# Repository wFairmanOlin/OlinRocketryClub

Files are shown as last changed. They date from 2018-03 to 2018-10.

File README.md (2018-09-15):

# OlinRocketryClub
Repo for a self-designed flight computer

## First Project - Phoenix I
1. 3-axis accelerometer
2. data storing functionality to SD card

## Second Project - Peregrine I
This board is intended to record flight data and transmit telemetry while maintaining a slim and lightweight profile.

### Main Components:
1. Barometer, Accelerometer, Gyroscope
2. Data storage to SD card
3. RF Transmitter
4. Battery

## How to Clone this Repo (Ubuntu)
1. Use the Ctrl+Alt+t command to open your terminal. 
2. Use the `cd` command to switch to the directory you want to save this repo in.
3. Copy and paste the code below into your terminal (hint: use Ctrl+Shift+v to paste into the terminal)
```
git clone https://github.com/wFairmanOlin/OlinRocketryClub.git
```

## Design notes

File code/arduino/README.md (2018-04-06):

## Most recent update
4/6/2018 This program currently only contains code for logging data to the SD card. 
We are successfully accessing IMU data, but we are having issues with the SD card reader 
itself - even the arduino example script will not run, suggesting there is a hardware or
wiring problem involved that needs to be resolve.

## REMAINING TODOS
  - Research and program apogee detection and decide how best to implement that. 
    Possibilities include integrating accelerometer data and relying on orientation of the IMU.
    For now, simply send power to a single pin to simulate releasing the parachute.
  - Acquire, prototype, and implement using a radio transmitter and receiver to send and receive RF beacon style data
  - Acquire, prototype, and implement using a radio transmitter and receiver to send and receive telemetry information.
  - Discretize steps into functions as soon as proof of concept has been achieved.

# Arduino Sketch
Prior to fabricating and testing a PCB for the rocket flight computer, we hope to create an arduino model of the system for base-level systems testing. To do so, we hope to write a quick arduino program, wire necessary hardware, and simulate a launch.

## The main goals of flight_computer.ino are:
1. Use an inertial measurement unit to determine when the rocket has reached apogee. When that has happened (i.e. when the velocity of the rocket is zero), deploy
        the parachute. 
2. Log telemetry data to the onboard SD card for study following retrieval. 
3. Use a radio transmitter as an RF beacon to aid retrieval efforts.
4. Use a radio transmitter to send telemetry data by means of packet radio. 

## The hardware components associated with this test include:
BreadBoard Components:
-accelerometer - https://www.adafruit.com/product/2019
-sd card slot  - https://www.sparkfun.com/products/544
-arduino uno - https://www.sparkfun.com/products/11021
-Breakout Radio Chips (2) - https://www.sparkfun.com/products/12775
-Sparkfun RF Link Transmitter - https://www.sparkfun.com/products/10534
-Sparkfun RF Link Receiver - https://www.sparkfun.com/products/10532

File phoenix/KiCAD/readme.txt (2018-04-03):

 

**********************************************************
*************  Important Instructions Follow  ************
**********************************************************
 
All files exported to: C:\EMA\ExportFolder\0\188490\Output\KiCAD\KiCAD\symbols.lib

After you have used Ultra Librarian to export library:
**************************************************
**To import your new library symbols into KiCad:**
**************************************************
1. Open KiCad.
2. On the program/tool list, go to Eeschema.
3. Select *Preferences* from the menu bar then select *Library*.
4. Click *Add* and choose the newly exported *.LIB* file.
5. You have now successfully imported your new symbol library!

**************************************************************
**To import your new library footprints/patterns into KiCad:**
**************************************************************
1. Open KiCad.
2. On the program/tool list, go to Pcbnew.
3. Follow the same steps as you would importing symbols, only this time select the *.kicad_mod* file.
4. You have now successfully imported your new footprint/pattern.

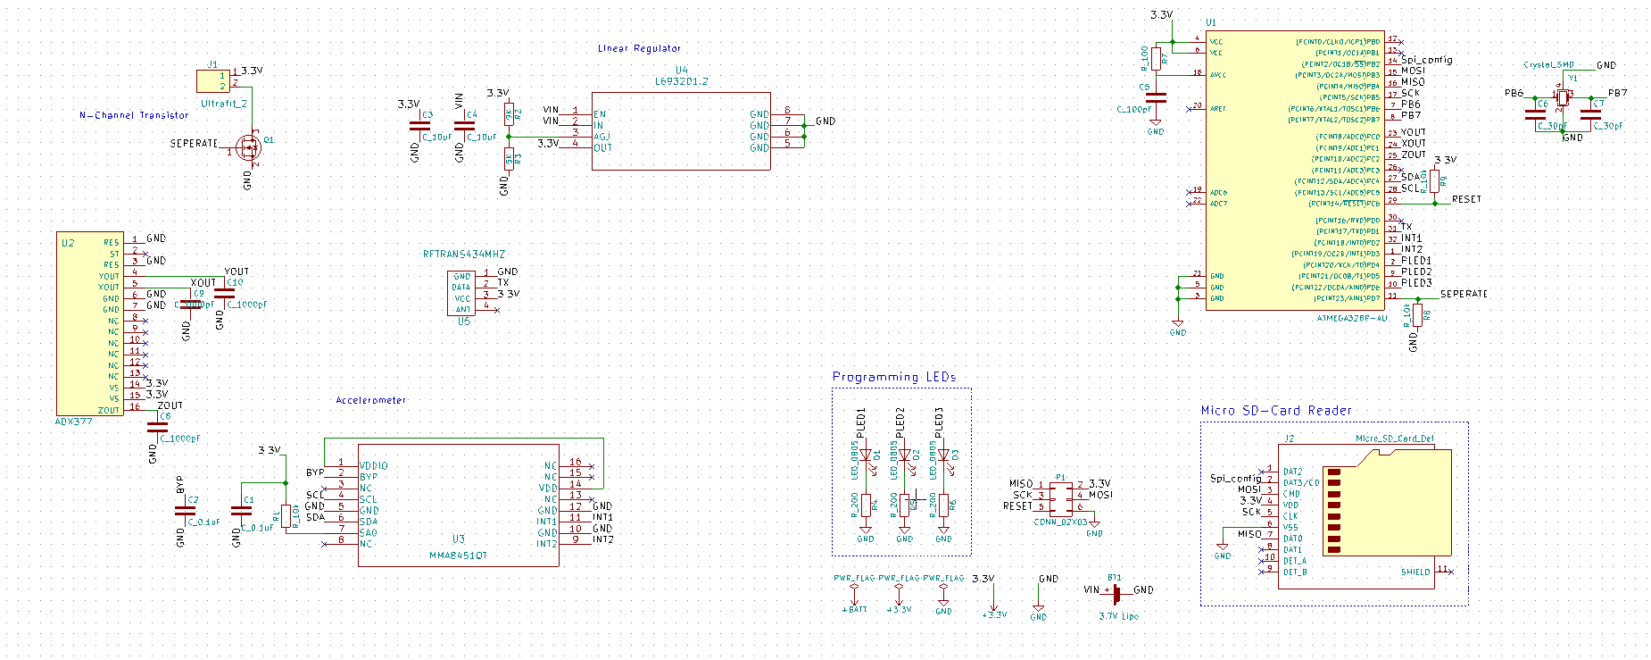
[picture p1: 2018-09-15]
phoenix/Schematic.png

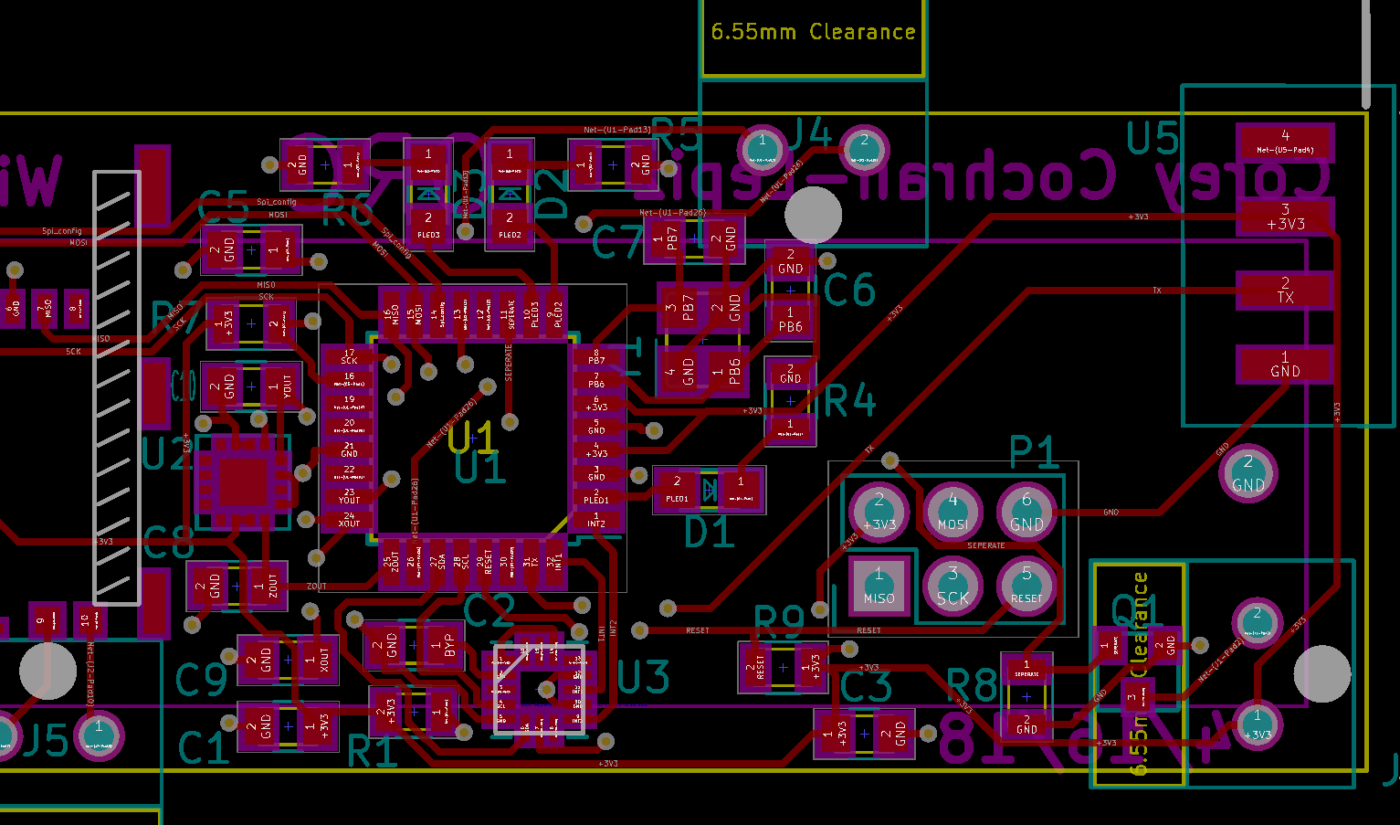
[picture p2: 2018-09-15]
phoenix/board.png

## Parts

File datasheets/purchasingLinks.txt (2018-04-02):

Purchasing Links
sd card slot  - https://www.digikey.com/product-detail/en/molex-llc/5045280892/WM12730CT-ND/5822266
gps chip      - https://www.adafruit.com/product/746
3.3V stepdown - https://www.digikey.com/product-detail/en/on-semiconductor/FAN5362UMP33X/FAN5362UMP33XCT-ND/3908079
--Option 2    - https://www.digikey.com/product-detail/en/stmicroelectronics/L6932D1.2TR/497-5724-1-ND/1299970
battery holder- https://www.digikey.com/product-detail/en/mpd-memory-protection-devices/BCAAPC/BCAAPC-ND/232723
MOSFET	      - https://www.digikey.com/product-detail/en/vishay-siliconix/SI4838DY-T1-E3/SI4838DY-T1-E3TR-ND/1656477
Batteries and
Charger       - https://www.amazon.com/EBL-Battery-Charger-Rechargeable-Batteries/dp/B076C4K4SR
MicroSD Card
Slot 	      - https://www.digikey.com/product-detail/en/molex-llc/5045280892/WM12730CT-ND/5822266

BreadBoard Components:
accelerometer - https://www.adafruit.com/product/2019
sd card slot  - https://www.sparkfun.com/products/544
cpu (sparkFun)- https://www.sparkfun.com/products/9061
AVR Programmer- https://www.sparkfun.com/products/9825
Breakout Radio Chips (need 2) - https://www.sparkfun.com/products/12775
Sparkfun RF Link Transmitter - https://www.sparkfun.com/products/10534
Sparkfun RF Link Receiver - https://www.sparkfun.com/products/10532

Spark plug via mosfet
http://forum.arduino.cc/index.php?topic=95811.0

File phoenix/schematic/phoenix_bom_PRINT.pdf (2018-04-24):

phoenix_bom_PRINT

Component | References Value | Quantity Per PCB
1 BT1 | 3.7V Lipo | 1
2 C1 C2 | C_0.1uF | 2
3 C8 C9 C10 C_1000pF | 3
4 C5 | C_100pF | 1
5 C3 C4 | C_10uF | 2
6 C6 C7 | C_30pF | 2
7 D1 D2 D3 | LED_0805 | 3
8J2 | Micro_SD_Card_Det | 1
9J1 | Ultrafit_2 | 1
10 P1 | CONN_02X03 | 1
11 Q1 | IRLML6344 | 1
12 R3 | 5K | 1
13 R2 | 9K | 1
14 R7 | R_100 | 1
15 R1 R8 R9 | R_10k | 3
16 R4 R5 R6 | R_200 | 3
17 U2 | ADX377 | 1
18 U1 | ATMEGA328P-AU | 1
19 U4 | L6932D1.2 | 1
20 U3 | MMA8451QT | 1
21 U5 | RFTRANS434MHZ | 1
22 Y1 | Crystal_SMD | 1

Component Groups:
Component Count:
Fitted Components:
Number of PCBs:
Total components:
Schematic Version:
Schematic Date:
BoM Date:
Schematic Source:
KiCad Version:

Datasheet | Package
http://datasheets.avx.com/X7RDielectric.pdf | Value
| Value
https://content.kemet.com/datasheets/KEM_C1003_C0G_SMD.pdf | Value
http://datasheets.avx.com/cx5r.pdf | Value
https://media.digikey.com/pdf/Data%20Sheets/Samsung%20PDFs/CL_Series_MLCC_ds.pdf Value
http://www.osram-os.com/Graphics/XPic9/00078860_0.pdf | Value
| Value
http://portal.fciconnect.com/Comergent//fci/drawing/67996.pdf | Value
https://www.infineon.com/dgdl/irlml6344pbf.pdf?fileId=5546d462533600a4015356689c44262c
https://www.seielect.com/Catalog/SEI-rncp.pdf | Value
http://www.bourns.com/data/global/pdfs/CRS.pdf | Value
https://www.seielect.com/Catalog/SEI-RMCF_RMCP.pdf | Value
https://support.epson.biz/td/api/doc_check.php?dl=brief_FA-238V_en.pdf | Value

MPN | MFN
478-3352-1-ND | Digi-Key
1276-6843-1-ND | Digi-Key
399-1122-1-ND | Digi-Key
478-5167-1-ND | Digi-Key
1276-1130-1-ND | Digi-Key
475-1410-1-ND | Digi-Key
WM11570-ND | Digi-Key
609-3234-ND | Digi-Key
RNCP0805FTD100RCT-ND | Digi-Key
CRS0805-FX-1002ELFCT-ND Digi-Key
RMCF0805JT200RCT-ND | Digi-Key
SER3686CT-ND | Digi-Key

PurchasingLink

https://www.digikey.com/products/en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

https://www.digikey.com/product-detail/en/molex-llc/1722861102/WM11570-ND/5344267https://www.digikey.com/product-detail/en/amphenol-fci/67997-206HLF/609-3234-ND/1878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

https://www.digikey.com/products/en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

https://www.digikey.com/products/en?keywords=SER3686CT-ND

PurchasingLinks

https://www.digikey.com/product-detail/en/infineon-technologies/IRLML6344TRPBF/IRLML6344TRPBFCT-ND/2538168

https://www.digikey.com/product-detail/en/analog-devices-inc/ADXL377BCPZ-RL7/ADXL377BCPZ-RL7CT-ND/3678489

https://www.digikey.com/products/en?mpart=MMA8451QT&v=568
https://www.sparkfun.com/products/10534

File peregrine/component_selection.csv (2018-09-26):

-------------------+-----------------+---------+------------------------+----------------+---------------------------
Component | Function | Price | Communication protocol | Max power draw | Notes
-------------------+-----------------+---------+------------------------+----------------+---------------------------
Atmel328PB | Microcontroller | 1.46/ea | n/a | 10mA@5v0
BMI088 | Accel+Gyro | 7.99/ea | SPI & I2C | 5.5mA@3v3 | gucci vibration rejection
ICG-20660L | Accel+Gyro | 8.27/ea | SPI & I2C | 3mA@3v3 | maybe ew????
BMP388 | Barometer | 3.93/ea | SPI & I2C | 0.68mA@3v3
MIC5504-3.3YM5-TR | 3v3 LDO | 0.11/ea | Screeching | 300mA | cheap!
-------------------+-----------------+---------+------------------------+----------------+---------------------------
 |  | 21.75 |  | <20mA
-------------------+-----------------+---------+------------------------+----------------+---------------------------

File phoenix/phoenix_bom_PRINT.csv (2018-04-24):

Component | References | Value | Quantity Per PCB | Datasheet | Package | MPN | MFN | PurchasingLink | PurchasingLinks
1 | BT1 | 3.7V Lipo | 1
2 | C1 C2 | C_0.1uF | 2 | http://datasheets.avx.com/X7RDielectric.pdf | Value | 478-3352-1-ND | Digi-Key | https://www.digikey.com/products/en?keywords=478-3352-1-ND
3 | C8 C9 C10 | C_1000pF | 3 |  | Value | 1276-6843-1-ND | Digi-Key | https://www.digikey.com/product-detail/en/samsung-electro-mechanics/CL21B102KB6WPNC/1276-6843-1-ND/5961702
4 | C5 | C_100pF | 1 | https://content.kemet.com/datasheets/KEM_C1003_C0G_SMD.pdf | Value | 399-1122-1-ND | Digi-Key | https://www.digikey.com/product-detail/en/kemet/C0805C101J5GACTU/399-1122-1-ND/411397
5 | C3 C4 | C_10uF | 2 | http://datasheets.avx.com/cx5r.pdf | Value | 478-5167-1-ND | Digi-Key | https://www.digikey.com/product-detail/en/avx-corporation/0805ZD106KAT2A/478-5167-1-ND/1913257
6 | C6 C7 | C_30pF | 2 | https://media.digikey.com/pdf/Data%20Sheets/Samsung%20PDFs/CL_Series_MLCC_ds.pdf | Value | 1276-1130-1-ND | Digi-Key | https://www.digikey.com/product-detail/en/samsung-electro-mechanics-america-inc/CL21C300JBANNNC/1276-1130-1-ND/3889216
7 | D1 D2 D3 | LED_0805 | 3 | http://www.osram-os.com/Graphics/XPic9/00078860_0.pdf | Value | 475-1410-1-ND | Digi-Key | https://www.digikey.com/products/en?keywords=475-1410-1-ND
8 | J2 | Micro_SD_Card_Det | 1
9 | J1 | Ultrafit_2 | 1 |  | Value | WM11570-ND | Digi-Key | https://www.digikey.com/product-detail/en/molex-llc/1722861102/WM11570-ND/5344267
10 | P1 | CONN_02X03 | 1 | http://portal.fciconnect.com/Comergent//fci/drawing/67996.pdf | Value | 609-3234-ND | Digi-Key | https://www.digikey.com/product-detail/en/amphenol-fci/67997-206HLF/609-3234-ND/1878491
11 | Q1 | IRLML6344 | 1 | https://www.infineon.com/dgdl/irlml6344pbf.pdf?fileId=5546d462533600a4015356689c44262c |  |  |  |  | https://www.digikey.com/product-detail/en/infineon-technologies/IRLML6344TRPBF/IRLML6344TRPBFCT-ND/2538168
12 | R3 | 5K | 1
13 | R2 | 9K | 1
14 | R7 | R_100 | 1 | https://www.seielect.com/Catalog/SEI-rncp.pdf | Value | RNCP0805FTD100RCT-ND | Digi-Key | https://www.digikey.com/products/en?keywords=RNCP0805FTD100RCT-ND
15 | R1 R8 R9 | R_10k | 3 | http://www.bourns.com/data/global/pdfs/CRS.pdf | Value | CRS0805-FX-1002ELFCT-ND | Digi-Key | https://www.digikey.com/products/en?keywords=CRS0805-FX-1002ELFCT-ND
16 | R4 R5 R6 | R_200 | 3 | https://www.seielect.com/Catalog/SEI-RMCF_RMCP.pdf | Value | RMCF0805JT200RCT-ND | Digi-Key | https://www.digikey.com/products/en?keywords=RMCF0805JT200RCT-ND
17 | U2 | ADX377 | 1 |  |  |  |  |  | https://www.digikey.com/product-detail/en/analog-devices-inc/ADXL377BCPZ-RL7/ADXL377BCPZ-RL7CT-ND/3678489
18 | U1 | ATMEGA328P-AU | 1
19 | U4 | L6932D1.2 | 1
20 | U3 | MMA8451QT | 1 |  |  |  |  |  | https://www.digikey.com/products/en?mpart=MMA8451QT&v=568
21 | U5 | RFTRANS434MHZ | 1 |  |  |  |  |  | https://www.sparkfun.com/products/10534
22 | Y1 | Crystal_SMD | 1 | https://support.epson.biz/td/api/doc_check.php?dl=brief_FA-238V_en.pdf | Value | SER3686CT-ND | Digi-Key | https://www.digikey.com/products/en?keywords=SER3686CT-ND
Component Groups:
Component Count:
Fitted Components:
Number of PCBs:
Total components:
Schematic Version:
Schematic Date:
BoM Date:
Schematic Source:
KiCad Version:

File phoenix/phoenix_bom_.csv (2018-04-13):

Component | Description | Part | References | Value | Footprint | Quantity Per PCB | Datasheet | Package | MPN | MFN | PurchasingLink | PurchasingLinks
1 | single battery cell | Battery_Cell | BT1 | 3.7V Lipo | battery_holder | 1
2 |  | C_0.1uF | C1 C2 | C_0.1uF | C_0805_OEM | 2 | http://datasheets.avx.com/X7RDielectric.pdf | Value | 478-3352-1-ND | Digi-Key | https://www.digikey.com/products/en?keywords=478-3352-1-ND
3 |  | C_100pF | C5 | C_100pF | C_0805_OEM | 1 | https://content.kemet.com/datasheets/KEM_C1003_C0G_SMD.pdf | Value | 399-1122-1-ND | Digi-Key | https://www.digikey.com/product-detail/en/kemet/C0805C101J5GACTU/399-1122-1-ND/411397
4 |  | C_10uF | C3 C4 | C_10uF | C_0805_OEM | 2 | http://datasheets.avx.com/cx5r.pdf | Value | 478-5167-1-ND | Digi-Key | https://www.digikey.com/product-detail/en/avx-corporation/0805ZD106KAT2A/478-5167-1-ND/1913257
5 |  | C_30pF | C6 C7 | C_30pF | C_0805_OEM | 2 | https://media.digikey.com/pdf/Data%20Sheets/Samsung%20PDFs/CL_Series_MLCC_ds.pdf | Value | 1276-1130-1-ND | Digi-Key | https://www.digikey.com/product-detail/en/samsung-electro-mechanics-america-inc/CL21C300JBANNNC/1276-1130-1-ND/3889216
6 |  | LED_0805 | D1 D2 D3 | LED_0805 | LED_0805_OEM | 3 | http://www.osram-os.com/Graphics/XPic9/00078860_0.pdf | Value | 475-1410-1-ND | Digi-Key | https://www.digikey.com/products/en?keywords=475-1410-1-ND
7 | Micro SD Card Socket with card detection pins | Micro_SD_Card_Det | J2 | Micro_SD_Card_Det | SD-Card | 1 | https://www.hirose.com/product/en/download_file/key_name/DM3/category/Catalog/doc_file_id/49662/?item_id=195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
8 |  | Ultrafit_2 | J1 | Ultrafit_2 | Ultrafit_2_RA | 1 |  | Value | WM11570-ND | Digi-Key | https://www.digikey.com/product-detail/en/molex-llc/1722861102/WM11570-ND/5344267
9 |  | CONN_02X03 | P1 | CONN_02X03 | Pin_Header_Straight_2x03 | 1 | http://portal.fciconnect.com/Comergent//fci/drawing/67996.pdf | Value | 609-3234-ND | Digi-Key | https://www.digikey.com/product-detail/en/amphenol-fci/67997-206HLF/609-3234-ND/1878491
10 | 200V Vds, N-Channel MOSFET, 2.6V Logic Level, TO-92 | IRLML6344 | Q1 | IRLML6344 | IRLML6344TRPBFCT-ND | 1 | https://www.infineon.com/dgdl/irlml6344pbf.pdf?fileId=5546d462533600a4015356689c44262c |  |  |  |  | https://www.digikey.com/product-detail/en/infineon-technologies/IRLML6344TRPBF/IRLML6344TRPBFCT-ND/2538168
11 |  | 5K | R3 | 5K | R_0805_OEM | 1
12 |  | 5K | R2 | 9K | R_0805_OEM | 1
13 |  | R_100 | R7 | R_100 | R_0805_OEM | 1 | https://www.seielect.com/Catalog/SEI-rncp.pdf | Value | RNCP0805FTD100RCT-ND | Digi-Key | https://www.digikey.com/products/en?keywords=RNCP0805FTD100RCT-ND
14 |  | R_10k | R1 R8 R9 | R_10k | R_0805_OEM | 3 | http://www.bourns.com/data/global/pdfs/CRS.pdf | Value | CRS0805-FX-1002ELFCT-ND | Digi-Key | https://www.digikey.com/products/en?keywords=CRS0805-FX-1002ELFCT-ND
15 |  | R_200 | R4 R5 R6 | R_200 | R_0805_OEM | 3 | https://www.seielect.com/Catalog/SEI-RMCF_RMCP.pdf | Value | RMCF0805JT200RCT-ND | Digi-Key | https://www.digikey.com/products/en?keywords=RMCF0805JT200RCT-ND
16 | TQFP32, 16k Flash, 1kB SRAM, 512B EEPROM | ATMEGA328P-AU | U1 | ATMEGA328P-AU | TQFP-32_7x7mm_Pitch0.8mm | 1 | http://www.atmel.com/images/atmel-8271-8-bit-avr-microcontroller-atmega48a-48pa-88a-88pa-168a-168pa-328-328p_datasheet.pdf
17 |  | L6932D1.2 | U4 | L6932D1.2 | L6932D1.2TR | 1
18 |  | MMA8451QT | U3 | MMA8451QT | MMA8451QT | 1 |  |  |  |  |  | https://www.digikey.com/products/en?mpart=MMA8451QT&v=568
19 |  | Crystal_SMD | Y1 | Crystal_SMD | Crystal_SMD_FA238 | 1 | https://support.epson.biz/td/api/doc_check.php?dl=brief_FA-238V_en.pdf | Value | SER3686CT-ND | Digi-Key | https://www.digikey.com/products/en?keywords=SER3686CT-ND
Component Groups: | 19
Component Count: | 28
Fitted Components: | 28
Number of PCBs: | 1
Total components: | 28
Schematic Version:
Schematic Date:
BoM Date: | Thu 12 Apr 2018 10:37:11 PM EDT
Schematic Source: | /home/william/Desktop/OlinRocketryClub/phoenix/phoenix.sch
KiCad Version: | Eeschema 4.0.7-e2-6376~58~ubuntu16.04.1

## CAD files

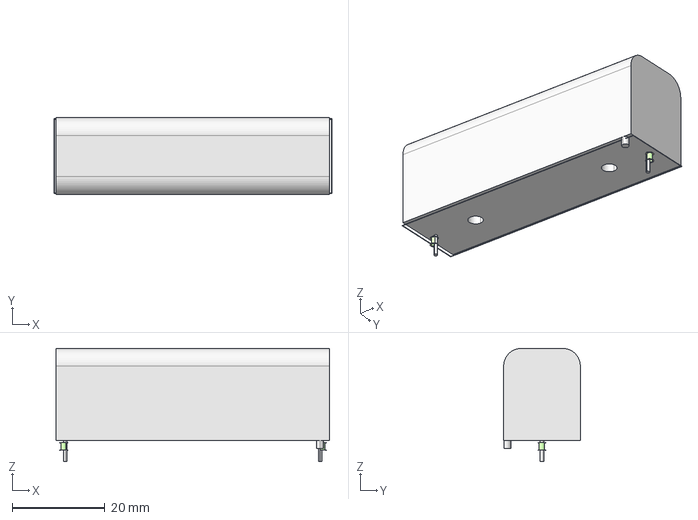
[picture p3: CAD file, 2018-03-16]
3d files/batter_holder/battery_holder.step
59.9 x 16.5 x 24.4 mm

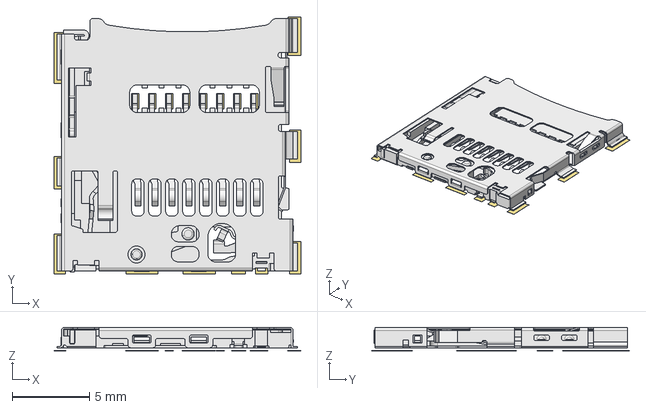
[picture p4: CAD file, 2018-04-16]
3d files/micro-sd/TopPads_sp.step
16.0 x 16.6 x 1.52 mm

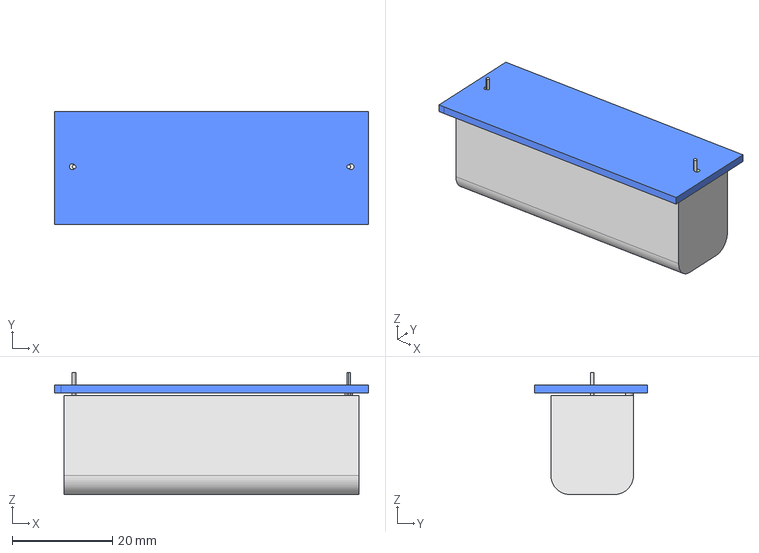
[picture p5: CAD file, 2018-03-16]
3d files/pcb.step
62.7 x 22.6 x 24.4 mm

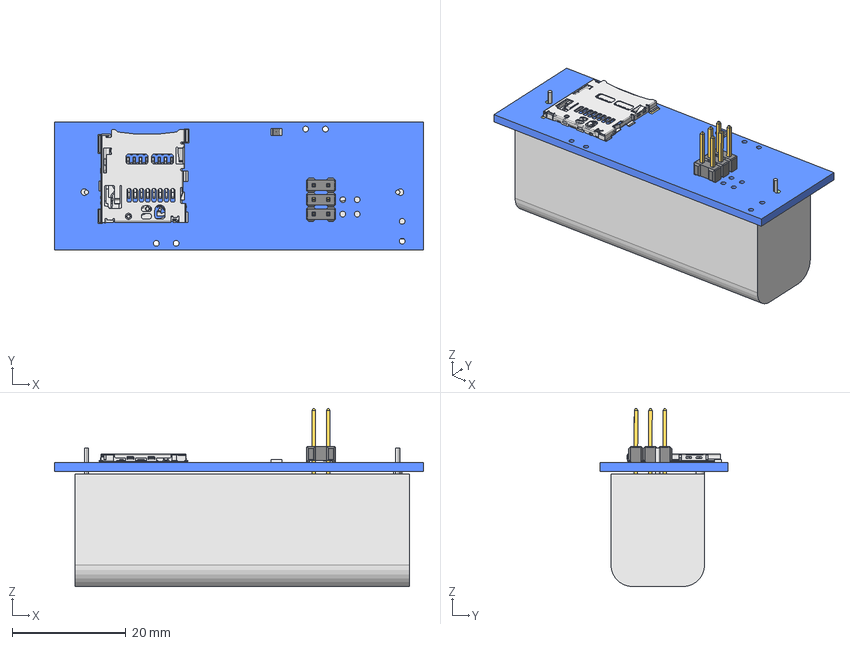
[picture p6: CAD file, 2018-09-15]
phoenix/PhoenixTwo.step
65.0 x 22.6 x 31.4 mm

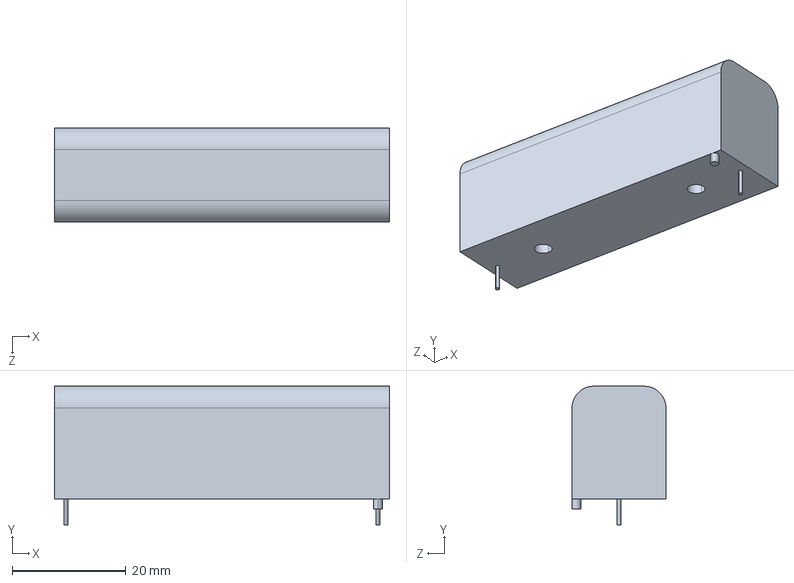
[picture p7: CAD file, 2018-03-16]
3d files/BHAA-3.STEP
58.9 x 24.4 x 16.5 mm

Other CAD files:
phoenix/phoenix.FCStd
phoenix/phoenix1.step

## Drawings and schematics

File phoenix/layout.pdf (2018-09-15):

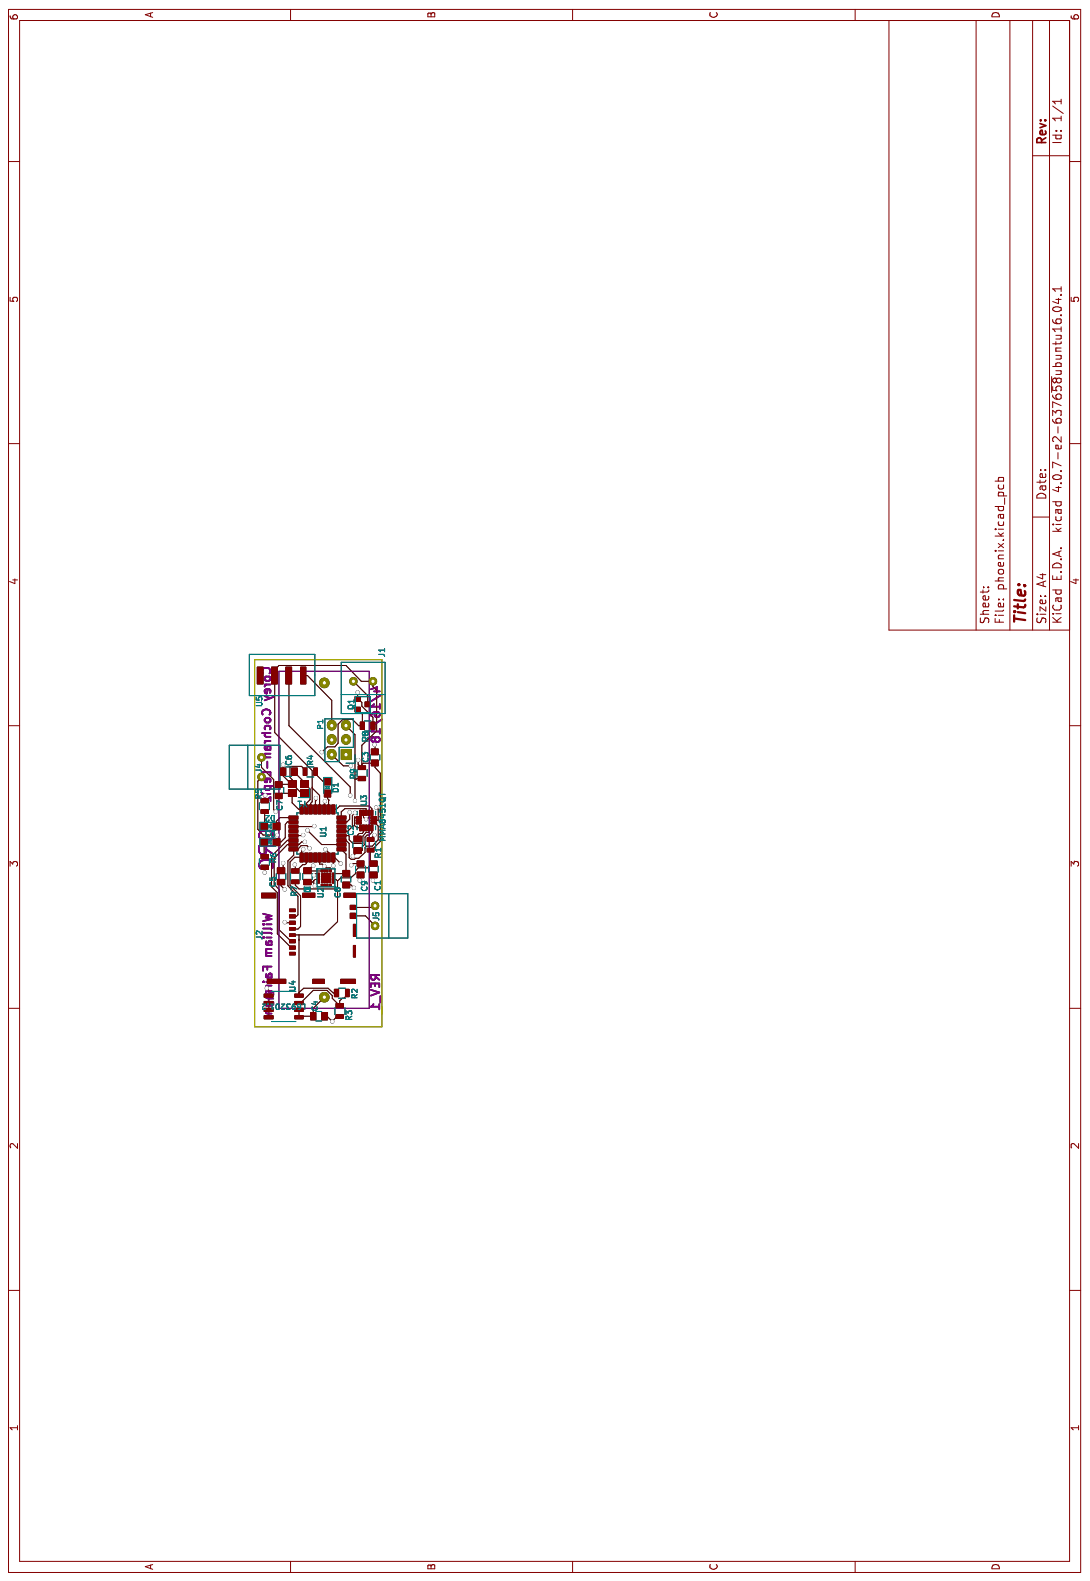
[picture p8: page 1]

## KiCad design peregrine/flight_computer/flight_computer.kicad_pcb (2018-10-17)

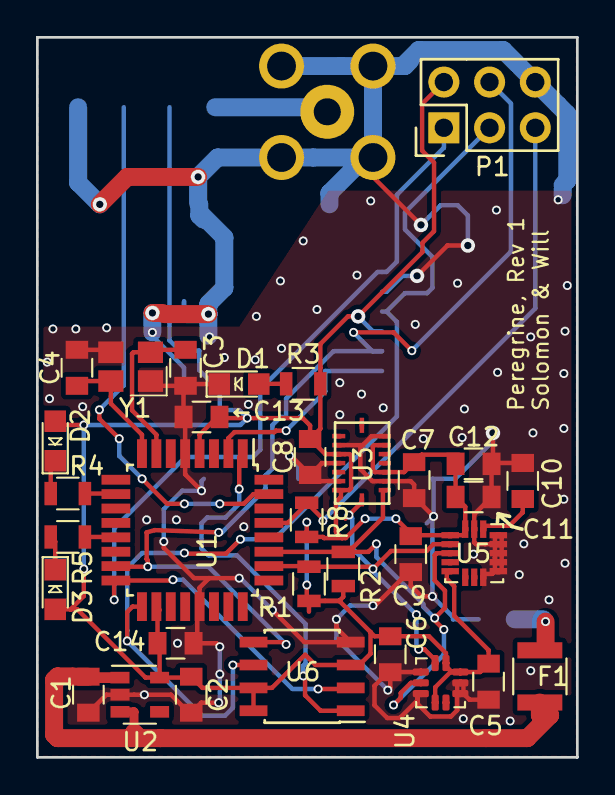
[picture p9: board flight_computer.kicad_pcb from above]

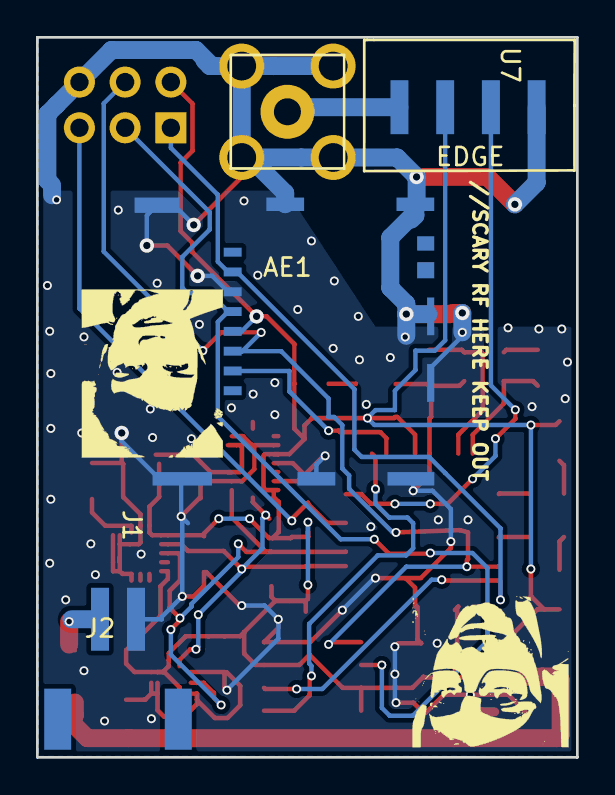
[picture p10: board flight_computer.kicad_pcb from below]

Board: 2 copper layers, 30.0 x 40.0 mm, 36 parts (4 on the bottom side), 22 nets.

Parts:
AE1: DS-SMA-EDGE-4; 5-1814400-1
C1, C2: C_1uF; C_0805_OEM
C3, C4: C_30pF; C_0805_OEM
C5, C6, C7, C8, C12, C14: C_0.1uF; C_0805_OEM
C9: 10nF; C_0805_OEM
C10: C_47uF; C_0805_OEM
C11: 2.2uF; C_0805_OEM
D1, D2, D3: LED_0805; LED_0805_OEM
F1: Fuse; Fuse_1210
J1: Micro_SD_Card_Det; SD-Card
J2: Conn_01x02_Male; JST_90DEG_2PIN
P1: CONN_02X03; Pin_Header_Straight_2x03
R1, R2: 4.7kR; R_0805_OEM
R3, R4, R5: R_200; R_0805_OEM
R8: R_10k; R_0805_OEM
U1: ATmega328PB-AU; TQFP-32_7x7mm_P0.8mm
U2: MIC5504-3.3YM5; SOT-23-5
U3: BMI088; BMI088-LGA16
U4: BMP388; ST_HLGA-10_2.5x2.5mm_P0.6mm_LayoutBorder3x2y
U5: ICG-20660; LGA-16_3x3mm_P0.5mm_LayoutBorder3x5y
U6: AT25SF041; SOIC-8_3.9x4.9mm_P1.27mm
U7: RFTRANS434MHZ
Y1: Crystal_SMD; Crystal_SMD_FA238
←C13: C_0.1uF; C_0805_OEM

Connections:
+3V3: C2.1, C5.1, C6.1, C7.2, C8.2, C9.1, C11.1, C12.1, C14.2, D2.2, D3.2, J1.4, P1.2, R1.1, R2.1, R3.2, R8.1, U1.4, U1.18, U2.5, U3.3, U3.7, U3.11, U3.14, U4.1, U4.6, U4.10, U5.1, U5.5, U5.16, U6.3, U6.7, U6.8, U7.3, ←C13.1
+BATT: C1.1, F1.1, U2.1, U2.3
/CS_FLASH: U1.1, U6.1
/CS_SD: J1.2, U1.2
/LED_B: R4.2, U1.10
/LED_R: R5.2, U1.13
/MISO: J1.7, P1.1, U1.16, U6.2
/MOSI: J1.3, P1.4, U1.15, U6.5
/RST: P1.5, R8.2, U1.29
/SCK: J1.5, P1.3, U1.17, U6.6
/SCL: R1.2, U1.26, U3.8, U4.2, U5.2
/SDA: R2.2, U1.27, U3.9, U4.4, U5.3
/TXD: U1.31, U7.2
/XTAL1: C3.1, U1.7, Y1.1
/XTAL2: C4.1, U1.8, Y1.3
GND: AE1.2, C1.2, C2.2, C3.2, C4.2, C5.2, C6.2, C7.1, C8.1, C9.2, C10.2, C11.2, C12.2, C14.1, D1.1, J1.6, J1.11, J2.2, P1.6, U1.5, U1.21, U2.2, U3.2, U3.4, U3.6, U3.10, U3.15, U4.3, U4.5, U4.8, U4.9, U5.8, U5.9, U5.10, U5.11, U5.12, U5.13, U5.15, U6.4, U7.1, Y1.2, Y1.4, ←C13.2
unnamed: AE1.1, U7.4
unnamed: C10.1, U5.14
unnamed: D1.2, R3.1
unnamed: D2.1, R4.1
unnamed: D3.1, R5.1
unnamed: F1.2, J2.1

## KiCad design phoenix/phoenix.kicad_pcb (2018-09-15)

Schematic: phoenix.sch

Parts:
BT1: 3.7V Lipo; battery_holder
C1, C2: C_0.1uF; C_0805_OEM; MPN 478-3352-1-ND
C3, C4: C_10uF; C_0805_OEM; MPN 478-5167-1-ND
C5: C_100pF; C_0805_OEM; MPN 399-1122-1-ND
C6, C7: C_30pF; C_0805_OEM; MPN 1276-1130-1-ND
C8, C9, C10: C_1000pF; C_0805_OEM; MPN 1276-6843-1-ND
D1, D2, D3: LED_0805; LED_0805_OEM; MPN 475-1410-1-ND
J1: Ultrafit_2; Ultrafit_2_RA; MPN WM11570-ND
J2: Micro_SD_Card_Det; SD-Card
P1: CONN_02X03; Pin_Header_Straight_2x03; MPN 609-3234-ND
Q1: IRLML6344; IRLML6344TRPBFCT-ND
R1, R8, R9: R_10k; R_0805_OEM; MPN CRS0805-FX-1002ELFCT-ND
R2: 9K; R_0805_OEM
R3: 5K; R_0805_OEM
R4, R5, R6: R_200; R_0805_OEM; MPN RMCF0805JT200RCT-ND
R7: R_100; R_0805_OEM; MPN RNCP0805FTD100RCT-ND
U1: ATMEGA328P-AU; TQFP-32_7x7mm_Pitch0.8mm
U2: ADX377; ADXL377
U3: MMA8451QT
U4: L6932D1.2; L6932D1.2TR
U5: RFTRANS434MHZ
Y1: Crystal_SMD; Crystal_SMD_FA238; MPN SER3686CT-ND

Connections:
+3V3: C1.1, C3.1, J1.1, J2.4 (VDD), P1.2, R1.2, R2.1, R7.1, R9.1, U1.4 (VCC), U1.6 (VCC), U2.14, U2.15, U4.4, U5.3
/BYP: C2.1, U3.2
/INT1: U1.32 ((PCINT18/INT0)PD2), U3.11
/INT2: U1.1 ((PCINT19/OC2B/INT1)PD3), U3.9
/MISO: J2.7 (DAT0), P1.1, U1.16 ((PCINT4/MISO)PB4)
/MOSI: J2.3 (CMD), P1.4, U1.15 ((PCINT3/OC2A/MOSI)PB3)
/PB6: C6.1, U1.7 ((PCINT6/XTAL1/TOSC1)PB6), Y1.1
/PB7: C7.1, U1.8 ((PCINT7/XTAL2/TOSC2)PB7), Y1.3
/PLED1: D1.2, U1.2 ((PCINT20/XCK/T0)PD4)
/PLED2: D2.2, U1.9 ((PCINT21/OC0B/T1)PD5)
/PLED3: D3.2, U1.10 ((PCINT22/OC0A/AIN0)PD6)
/RESET: P1.5, R9.2, U1.29 ((PCINT14/~RESET~)PC6)
/SCK: J2.5 (CLK), P1.3, U1.17 ((PCINT5/SCK)PB5)
/SCL: U1.28 ((PCINT13/SCL/ADC5)PC5), U3.4
/SDA: U1.27 ((PCINT12/SDA/ADC4)PC4), U3.6
/SEPERATE: Q1.1, R8.1, U1.11 ((PCINT23/AIN1)PD7)
/Spi_config: J2.2 (DAT3/CD), U1.14 ((PCINT2/OC1B/~SS~)PB2)
/TX: U1.31 ((PCINT17/TXD)PD1), U5.2
/VIN: BT1.1 (+), C4.1, U4.1, U4.2
/XOUT: C9.1, U1.24 ((PCINT9/ADC1)PC1), U2.5
/YOUT: C10.1, U1.23 ((PCINT8/ADC0)PC0), U2.4
/ZOUT: C8.1, U1.25 ((PCINT10/ADC2)PC2), U2.16
unnamed: C5.1, R7.2, U1.18 (AVCC)
unnamed: D1.1, R4.1
unnamed: D2.1, R5.1
unnamed: D3.1, R6.1
unnamed: J1.2, Q1.3
unnamed 29: J2.9 (DET_B); also elsewhere on the board
unnamed 30: J2.10 (DET_A); also elsewhere on the board
unnamed: R1.1, U3.7
unnamed: R2.2, R3.1, U4.3
unnamed 34: U1.13 ((PCINT1/OC1A)PB1); also elsewhere on the board
unnamed 38: U1.26 ((PCINT11/ADC3)PC3); also elsewhere on the board
unnamed: U3.1, U3.14

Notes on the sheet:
Programming LEDs
Micro SD-Card Reader
Accelerometer
Linear Regulator
N-Channel Transistor

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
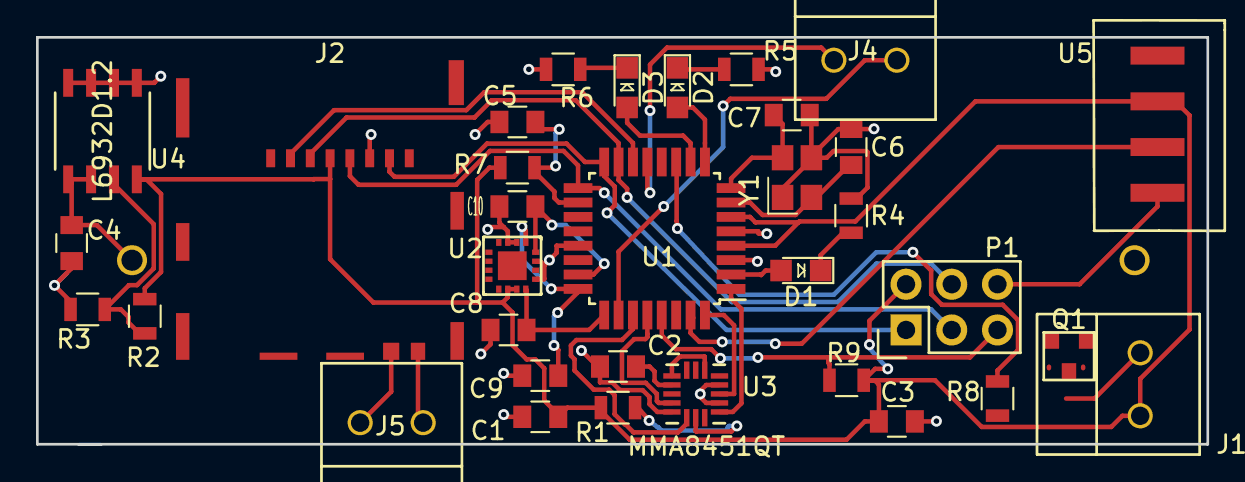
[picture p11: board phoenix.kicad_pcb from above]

Board: 2 copper layers, 65.0 x 22.6 mm, 35 parts (1 on the bottom side), 35 nets.

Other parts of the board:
J4, J5: Ultrafit_2

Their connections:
unnamed 29: J5.2; also elsewhere on the board
unnamed 30: J5.1; also elsewhere on the board
unnamed 34: J4.1; also elsewhere on the board
unnamed 38: J4.2; also elsewhere on the board

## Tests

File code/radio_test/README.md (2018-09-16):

This folder contains testing code and instructions for setting up the transmitter and receiver for testing antennas used to retrieve the rocket.
# Parts Used
The transmitter, receiver, and antenna under test are all optimized for the 434 MHz band.
For breadboard testing, we used [the sparkfun beacon receiver](https://www.sparkfun.com/products/10532) and [transmitter](https://www.sparkfun.com/products/10534). Antennas under test are wired directly to the receiver or transmitter. 
# Test Setup
Both the receiver and transmitter chips included handle actual modulation and signal generation and have connectors for antennas. Antenna evaluation running the respective test program on an arduino for each module and connecting a controlled antenna to one module and an experimental one to the other. Because the primary goal of RF beacon functionality is rocket retrieval, we generally attach the experimental antenna to the receiver and a simple wire or dipole to the transmitter.

# TODO
## Software
* Remove dependency on virtualwire library
* Incorporate signal strength indicator if possible - perhaps using RTL-SDR on receive side.
* Start to develop beacon code for ATMEGA after determining needed functionality
## Antenna Development
9/16 Antenna: Functional, but not highly directional. Could use additional spacing changes and maybe a coaxial cable to plug into an RTL-SDR.

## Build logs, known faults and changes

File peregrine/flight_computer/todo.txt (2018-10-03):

-> microSD

-> TODO: is 5v from programmer gonna fry board

-> Create 2.2uF & 10nF caps in rocket lib => digikey link
-> Create 5.6ohm & 68ohm resistors in rocket lib => digikey link

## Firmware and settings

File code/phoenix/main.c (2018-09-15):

#include <avr/io.h>
#include <util/delay.h>
#include <avr/interrupt.h>


#define F_CPU           4000000UL
#define PORT_LED        PORTD
#define REG_LED         DDRD
#define LED1            PD4
#define LED2            PD5
#define LED3            PD6

#define PORT_A          PORTC
#define REG_A           DDRC
#define YOUT            PC0
#define XOUT            PC1
#define ZOUT            PC2

#define FLAG_EMATCH     0

uint8_t gFlag = 0x00;

uint8_t gY = 0x00;
uint8_t gX = 0x00;
uint8_t gZ = 0x00;

unsigned long gCounter = 0x00;

/* TODO FOR WEDNESDAY */
//Get timer working
//Write to sd-card
//Get transistor working
//Calibrate accelerometer data
//Create function for appogee using accel data
//https://electronics.stackexchange.com/questions/66145/avr-how-to-program-an-avr-chip-in-linux

ISR(TIMER0_COMPA_vect){
    //TODO fix
    //Currently ticks at 4hz
    gCounter++;
    if (gCounter > 60){
        gFlag |= _BV(FLAG_EMATCH);
    }
    if(gCounter > 80){
        gFlag |= _BV(3);
    }

}

void initTimer(void) {
    //TODO
    //FOR 16M1, configure for 328P
    TCCR0A = _BV(WGM01);    // Set up 8-bit timer in CTC mode
    TCCR0B = 0x05;          // clkio/1024 prescaler
    TIMSK0 |= _BV(OCIE0A);
    OCR0A = 0xFF;
}


void initADC(void) {
    //Get the Analog to Digital Converter started (ADC)
    ADCSRA |= _BV(ADEN) | _BV(ADPS2) | _BV(ADPS0);

    //Enable interal reference voltage
    // ADCSRB |= _BV(AREFEN);

    //Set internal reference voltage as AVcc
    ADMUX |= _BV(REFS0);

    //Reads by default from ADC0 (pin 11)
    //This line is redundant. The timer
    ADMUX |= _BV(0x00);
}

void readAC(int test){
    ADMUX = _BV(REFS0);
    ADMUX |= 0;
    ADCSRA |= _BV(ADSC);
    loop_until_bit_is_clear(ADCSRA, ADSC);
    gY = (uint8_t) (ADC >> 2);


    ADMUX = _BV(REFS0);
    ADMUX |= 1;
    ADCSRA |= _BV(ADSC);
    loop_until_bit_is_clear(ADCSRA, ADSC);
    gX = (uint8_t) (ADC >> 2);


    ADMUX = _BV(REFS0);
    ADMUX |= 2;
    ADCSRA |= _BV(ADSC);
    loop_until_bit_is_clear(ADCSRA, ADSC);
    gZ = (uint8_t) (ADC >> 2);

    if(test==1){
        if(gX > 128){
            PORT_LED |= _BV(LED1);
        } else {
            PORT_LED &= ~_BV(LED1);
        }

        if(gY > 128){
            PORT_LED |= _BV(LED2);
        } else {
            PORT_LED &= ~_BV(LED2);
        }

        if(gZ > 128){
            PORT_LED |= _BV(LED3);
        } else {
            PORT_LED &= ~_BV(LED3);
        }
    }
}

void triggerEMatch(void){

}

int main (void) {

    sei();
    initADC();
    initTimer();


    REG_LED |= _BV(LED1) | _BV(LED2) | _BV(LED3);
    DDRD |= _BV(PD7);
    PORT_LED |= _BV(LED1);
    PORT_LED |= _BV(LED3);
    // uint8_t count = 0;
    while(1) {
        // count++;
        readAC(0);




    }
}

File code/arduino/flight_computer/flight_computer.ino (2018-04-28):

// Olin Rocketry Flight Computer Sketch for drop test.

#include <Adafruit_MMA8451.h>
#include <Adafruit_Sensor.h>
#include <SD.h>
#include <Wire.h>

File telemetry;
Adafruit_MMA8451 imu = Adafruit_MMA8451();

void setup() {
  // Sensor and Serial Initialization
  Serial.begin(9600);
  // Kick off the IMU's datalogging.
  if (!imu.begin()) {
    Serial.println("IMU initialization failed!");
    while (1);
  }
  // Set IMU range.
  imu.setRange(MMA8451_RANGE_2_G);
  // Kick off SD Card initialization.
  pinMode(10, OUTPUT);
  if (!SD.begin(10)) {
    Serial.println("SD Card initialization failed!");
    while (1);
  }

  //Variable Intialization
  // Boolean about whether or not the launch has begun, needed for task 0.
  bool started = false; 
  // Float value of previous timestamp, needed for task 0.
  float previous_timestamp = 0.0;
  // Float value of previous velocity value, needed for task 0.
  float previous_velocity = 0.0;
  // TODO : Determine actual cutoff before apogee.
  // Integer time cutoff for apogee - deploy parachute. 
  int cutoff = 6000;
  // Zero velocity threshold 
  float zero_velocity_threshold = .500;
  float current_timestamp;
  float current_velocity;
  float refresh_rate = 500;
  Serial.println("Setup complete.");
}

void loop() { 
  // Taken from adafruit documentation for printing sensor events.
  sensors_event_t event; 
  imu.getEvent(&event);
  Serial.println(event.timestamp);
  telemetry.print(event.timestamp);

  //Task 0: Detect apogee, and deploy parachute.
  // Calculate velocity using a right-leaning Reimann sum.
  current_timestamp = millis()
  float current_velocity = ((sqrt(pow(imu.x, 2) + pow(imu.y, 2)) + previous_velocity)/2) * (current_timestamp - previous_timestamp);
  previous_acceleration = current_velocity;
  previous_timestamp = current_timestamp;
  
  // Task 1: Log IMU data to SD card. 
  // TODO : Make it such that the telemetry data filename can be something useful every time.

  if (abs(current_velocity) < zero_velocity_threshold) {
    telemetry.println("Deploying parachute.")
    // TODO : DO WHATEVER'S NEEDED TO DEPLOY THE PARACHUTE. Probably just apply voltage to some pin...
  }
  // Set up the telemetry file.
  telemetry = SD.open("data.txt", FILE_WRITE);
  // To read raw data, just access imu.x, imu.y, imu.z.
  // Here, we can leverage the fact that our imu is configured for i2c
  // and go ahead and use the built-in sensor events from the adafruit 
  // library. These are nicely regularzied for us.  
  Serial.print("X: \t"); Serial.print(event.acceleration.x); Serial.print("\t");
  Serial.print("Y: \t"); Serial.print(event.acceleration.y); Serial.print("\t");
  Serial.print("Z: \t"); Serial.print(event.acceleration.z); Serial.print("\t");
  Serial.println("m/s^2 ");
  
  // Assuming the file has been opened correctly, go ahead and save data to the SD card.
  if (telemetry) {
    telemetry.print("Time: \t"); telemetry.print(current_timestamp); telemetry.print("\t");
    telemetry.print("X: \t"); telemetry.print(event.acceleration.x); telemetry.print("\t");
    telemetry.print("Y: \t"); telemetry.print(event.acceleration.y); telemetry.print("\t");
    telemetry.print("Z: \t"); telemetry.print(event.acceleration.z); telemetry.print("\t");
    telemetry.println("m/s^2");
   } else {
    // if the file didn't open, print an error to the serial:
    Serial.println("Error opening text file. Sad.");
  }
  /* Get the orientation of the sensor */
  uint8_t o = imu.getOrientation();
  switch (o) {
    case MMA8451_PL_PUF: 
      telemetry.println("Orientation: Portrait Up Front");
      break;
    case MMA8451_PL_PUB: 
      telemetry.println("Orientation: Portrait Up Back");
      break;    
    case MMA8451_PL_PDF: 
      telemetry.println("Orientation: Portrait Down Front");
      break;
    case MMA8451_PL_PDB: 
      telemetry.println("Orientation: Portrait Down Back");
      break;
    case MMA8451_PL_LRF: 
      telemetry.println("Orientation: Landscape Right Front");
      break;
    case MMA8451_PL_LRB: 
      telemetry.println("Orientation: Landscape Right Back");
      break;
    case MMA8451_PL_LLF: 
      telemetry.println("Orientation: Landscape Left Front");
      break;
    case MMA8451_PL_LLB: 
      telemetry.println("Orientation: Landscape Left Back");
      break; 
  // TODO : TASK 3: RF Beacon
  // TODO : TASK 4 : Packet Radio
  
  }
  Serial.println();
  telemetry.close();
  
  delay(refresh_rate);
}

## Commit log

2018-02-19 started a kicad project and added datasheets for some components
    [phoenix.kicad_pcb, phoenix.sch]
2018-02-26 added a list of purchasing links for a bread board flight computer
2018-03-12 Add PCB cad file
    -Start footprints.pretty folder
    -Add battery_holder footprint
    -Add programming header footprint
    [BHAA-3.STEP, battery_holder.step, pcb.step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]
2018-03-13 Add link to sparkplug with mosfet
2018-03-16 added components
    [phoenix.sch]
2018-03-27 added more components to the library and also included all of formula's components to the library
    [phoenix.sch]
2018-03-28 Updated schematic
    [phoenix.sch]
2018-04-03 added components to board
    [phoenix.sch]
2018-04-04 added more parts
    [phoenix.sch]
2018-04-06 created documentation for flight computer
    there were too many notes at the top of the arduino code...
2018-04-06 Added basic start to arduino code
    Includes IMU to SD card datalogging and note much else
2018-04-12 Added external oscillator
    [phoenix.sch]
2018-04-12 Edited schematic and added footpring
    [phoenix.sch]
2018-04-12 new footprints
2018-04-12 Started layout
    [phoenix.kicad_pcb, phoenix.sch]
2018-04-12 fixed power transistor. Added to layout
    [phoenix.kicad_pcb, phoenix.sch]
2018-04-13 more partsgit add *
    [phoenix.sch, phoenix_bom_.csv]
2018-04-13 added new accelerometer
    [phoenix.sch]
2018-04-13 added more labels
    [phoenix.sch]
2018-04-15 more components
    [phoenix.sch]
2018-04-15 fixed footprint
2018-04-16 Draft layout
    Added:
    -changes to layout
    -drafted tracing
    -modified some footprints
    -added 3d-file for micro-sd-card slot
    [TopPads_sp.step, phoenix.kicad_pcb, phoenix.sch]
2018-04-16 Update layout and tracing
    [phoenix.kicad_pcb]
2018-04-16 Fix references
    stuuf
    [phoenix-B.Cu.gbr, phoenix-B.Mask.gbr, phoenix-B.SilkS.gbr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]
2018-04-24 Start C code for board
    [phoenix.kicad_pcb, phoenix_bom_PRINT.csv]
2018-04-29 Update non-working code for computer
    [PhoenixTwo.step, phoenix.FCStd, phoenix1.step]
2018-05-01 First good code for board
2018-05-02 Add schematic pictures
2018-09-15 update to kicad 5
    [phoenix-2018-09-15-11-02-53.sch, phoenix.sch]
2018-09-19 Component selection
    [component_selection.csv]
2018-09-26 Updated schematic & footprints
    [flight_computer.kicad_pcb, flight_computer.sch]
2018-10-03 Finished schematic + footprints ==> starting on layout
    [flight_computer.sch]
2018-10-17 Final rev?
    [flight_computer.kicad_pcb, flight_computer.sch]
2018-10-17 Jesus help me
    [flight_computer.kicad_pcb]

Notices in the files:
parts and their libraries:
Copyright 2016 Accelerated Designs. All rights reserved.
